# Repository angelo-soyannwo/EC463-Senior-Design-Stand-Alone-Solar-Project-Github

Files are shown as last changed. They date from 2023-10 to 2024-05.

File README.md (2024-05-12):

# Sol: An Alternative Off-grid Solar Configuration

## Quick-Start Info

### Structural Hardware

The hardware of our system consists of a frame with solar panels on either side, and a pair of reflectors in between. These reflectors slide diagonally up and down, and sideways along the rails of the frame, moved a stepper motor on either side and ball screws as the linear actuator. 3D printed components are used for interface between different parts, such as the stepper motor mount, sliding face plates, and ball screw rod attachers. Housing has also been developed for our PCBs, battery, and solar charge controller.

### Electronic Hardware

Most of our electronic pieces fit on a PCB. The light sensors and limit switches fit on the solar panels and rails of the frame respectively. The components on the PCB are: 2 Rpi Pico W's, a motor driver, buttons for Pico reset and manual motor control, 2 current sensors, and a temperature sensor. A Renogy solar charge controller is used externally to charge our battery with the solar panel, as well as power our system along with any other load.

### Control Pico Software

Our control software controls the movement of our reflectors through the stepper motors. The two stepper motors are connected in parallel to just one motor driver, so the code is made simple. Upon startup, the program moves the reflectors to their bottom-most position, where it will hit the bottom limit switch and begins tracking its position through step count. As of now, the position tracking is not an integral part of the system, since the program allows the reflectors to move upwards or downwards until they hit the limit switches; the position can be used for other purposes in the future. After startup and every ten seconds, the reflectors will check the light sensor readings, move a certain number of steps in a direction determined from the previous iteration, and check the light reading again. Based on the difference between the two readings, it will continue to move in the direction with more light or stop moving when the difference no longer passes a certain threshold. All of these parameters can be set in the software, including time between iterations and light difference threshold. Additionally, data from the light sensors are sent to our database on each iteration.

### Monitoring Pico Software

The monitoring software keeps track of charge and discharge current and voltage, and temperature of our system within the housing. It does so using two current/voltage sensor and one temperature sensor. The program first connects to WiFi, then begins the normal operation during which it sends data to our database every few seconds.

### Web Application

The web application uses a MERN stack (MongoDB, Express.js, React, Node.js). The web app takes data from our database on MongoDB, which in turn has data uploaded from our Pico servers. The user interface of the web app allows users to create an account, create arrays of our solar modules, and monitor solar panel output power, solar irradiation, and temperature across time. If any anomaly is detected, the user will receive an email such that they can check up on the system as soon as they can.

Link to Web Application: https://sol-ec-464-team-15.netlify.app/

Solar Array Id: 65539e775435e37264e3e6ff

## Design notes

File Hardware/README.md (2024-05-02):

# Hardware Documentation
## Overview
The hardware in SOL is segmented into two parts :
1. Structure & Housing
2. Electronics

The Structure & Housing consists of the solar-panels, the reflector system (mentioned in more detail below), the aluminum-gantry for mounting, and the various housings that contain the electronics & battery. 

The Electronics consist of the sensors, microcontrollers, motor driver, the Solar Charge Controller, and the PCB's that connect them. These monitor the structure, log data, then control the system based on the feedback received from the sensors.

## Structure & Housing
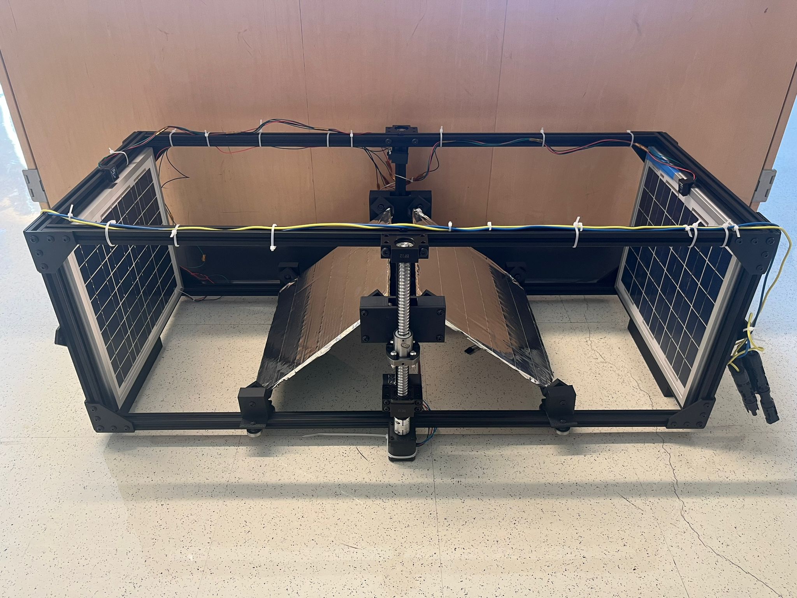
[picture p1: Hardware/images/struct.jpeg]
SOL Aluminum Structure


Above is the structure, which consists of the reflector system, the solar-panels, and the aluminum-gantry. 

### Aluminum Gantry
These are standard aluminum extrusions that can be purchased from various retailers. The original rods were 40in in length, and were machined down to an appropriate size. The size of the structure was determined by the size of the panels, and was designed such that the reflectors have enough room to cover their entire range of motion. More on this is detailed in the reflector system below. The structure is held together via aluminum brackets & screw joints.

### Solar Panels
The panels used in our design serve as proof-of-concept. As such, we were not bound to a particular power/size requirement, and thus chose panels that were provided to us by our client. The panels are 14x12 in, and have a maximum power output of 20W. 

### Reflector System
In order to explore an alternative offgrid solar-configuration, we designed a novel reflector system. The system is composed of 3D printed parts, and uses ball bearings to move about the aluminum rails. The movement of the system was inspired by 3D Printers, which use bearings to achieve precise motion. In our case, we did not need precise movement, however the notion of movement was still appealing thanks to its simplicity.

The system works as follow : 
- The stepper motors are connected to a motor driver on the PCB. 
- The motors themselves are connected to a ballscrew via a coupler. 
- The rotation of the motor turns the ballscrew clockwise/counter clockwise.
- The ballscrew is fitted onto the aluminum gantry via 3D printed mounts, and bolted joints.
- There is a printed faceplate that snaps onto the ballscrew. 
- With rotation limited, the faceplate translates upwards or downwards with the threads on the ballscrew.
- Rotational movement is turned into linear motion, which allows the connected reflectors to move radially.
- The ends of the reflectors are also connected to the gantry via sliding face-plates.

Below are renders of all the parts used in the project. These were modelled in Fusion 360 by Majid Al-Muhaideb.

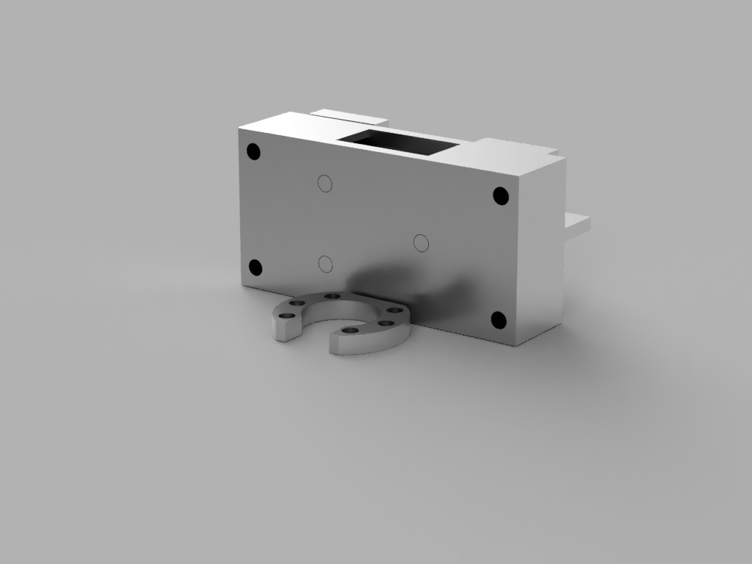
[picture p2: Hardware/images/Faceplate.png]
Faceplate Render

Faceplate Render. Snaps onto ballscrew.
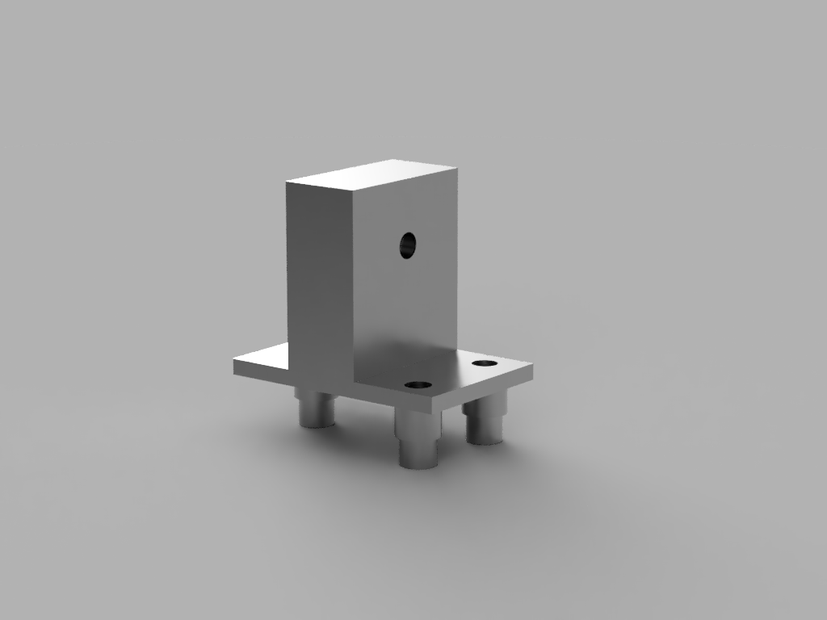
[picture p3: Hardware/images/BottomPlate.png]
Bottom Faceplate

Bottom Faceplate. bolted to the reflectors.
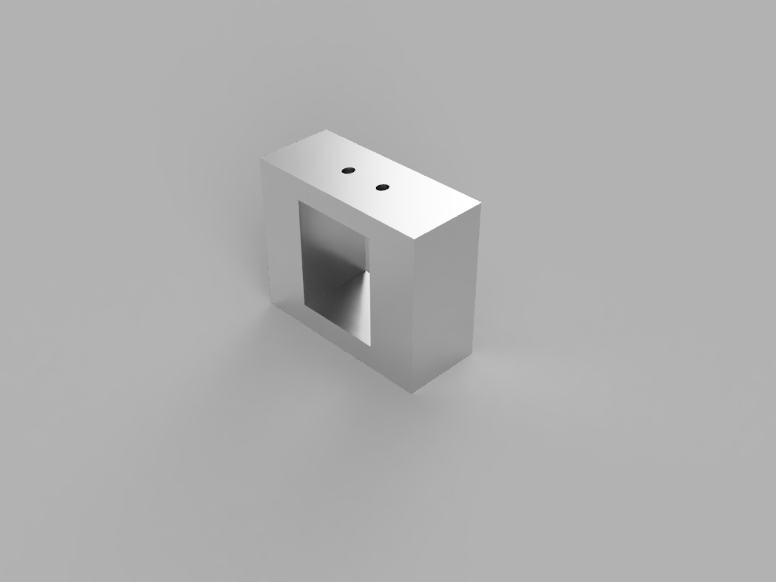
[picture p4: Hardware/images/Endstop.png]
Endstop mount

Endstop mount. Used to secure end-stops to end of the range.
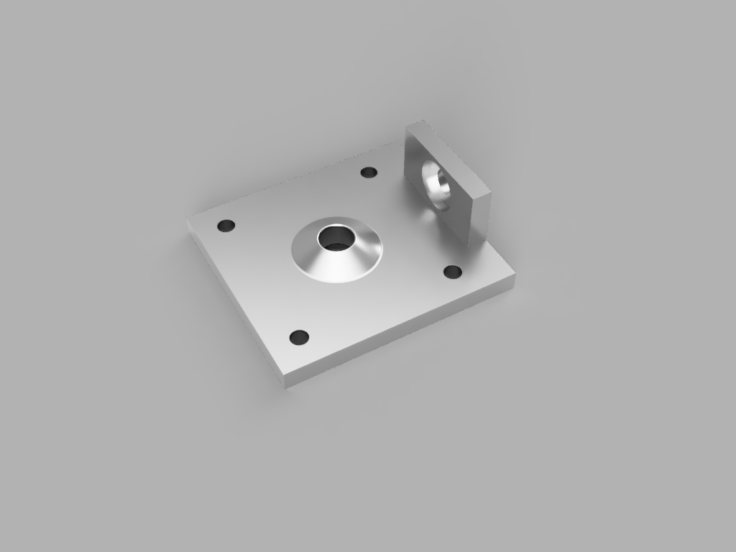
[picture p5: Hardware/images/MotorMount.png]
Motor mount

Motor mount. Used to secure motor to the structure.
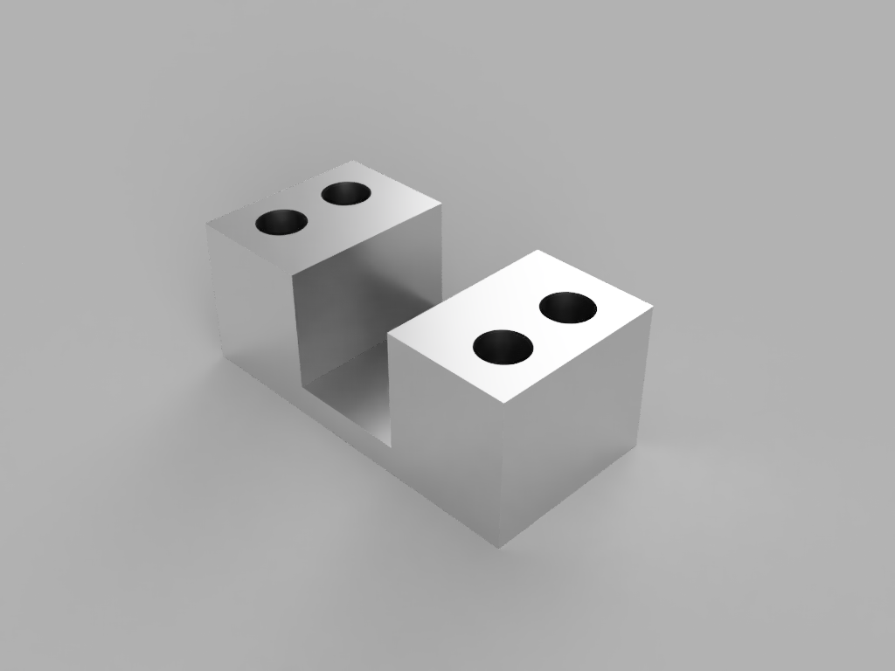
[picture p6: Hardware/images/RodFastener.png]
Rod fastener

Rod fastener. Secures rod to the structure.

The parts were printed in Black ELEGOO PLA. PETG or ABS is preferable due to their stronger mechanical properties, but both require more tuning to print properly, and are not as easy to setup as PLA. The parts dont experience a lot of mechanical stress, so it should not be an issue if used for the purposes of demonstration.

The print settings are as follows :

*Infill - 20 - 40 %*

*Infill Pattern - Gyroid*

*Print Supports - Auto, Normal*

*Walls - 3 inner walls*

Settings can be adjusted as the user sees fit, especially since each printer is tuned differently.

## Electronics
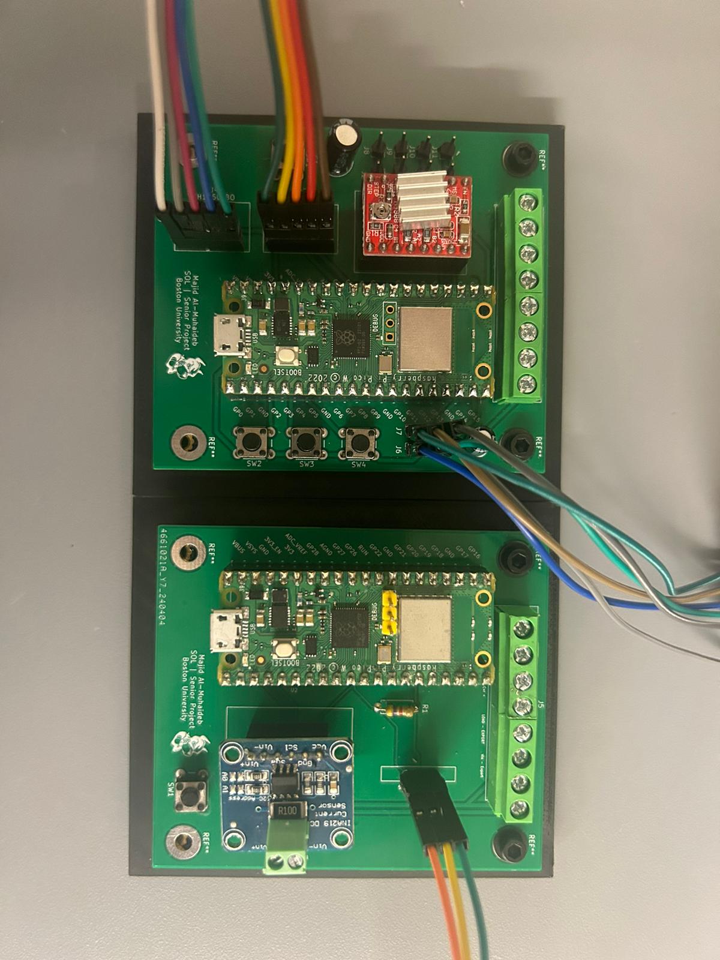
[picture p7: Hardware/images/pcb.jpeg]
Printed circuit boards


Above are the electronics used in the project. The image is a little outdated, as we've combined the two boards into one, but the electronics on them are the same, and the change is for convinence only. The electronics are divided into two subsections :

1. Monitoring : Consists of sensors that monitor current, temperature, voltage, and luminecence. The data these sensors collect is managed by a Pi Pico microcontroller.

2. Control : Consists of a motor driver that sends signals to the stepper motors. The driver is controlled by a Pi Pico Microcontroller.

The connections of these electronics can be examined in more detail in the schema folder, which contains the PCB schematic & design.

The following are some notes that should be regarded towards the PCB : 
Netlist Explanations :
 - Load + = Load from solar charge controller
 - Load - = Return path from solar charge controller. This is ground.
 - Vin P + = Positive from solar panels
 - Vin P - = Negative from solar panels
 - 3.3V_M = 3.3V from monitoring pico
 - 3.3V_C = 3.3V from control pico
 - 5V = Input from a 12V-5V converter. This is an external component
 - VCC = Vin -  from the INA219. This is 12V, and is idential to Load+.

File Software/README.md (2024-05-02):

# Software Documentation

## Overview
The software consists of three parts:
1. Reflector Control System
2. Monitoring System
3. Web Application

The control system is written in MicroPython and is uploaded to the Rpi Pico W designated for controls on the PCB. The program controls the rotation of the stepper motors to move the reflectors up and down. It does so through an algorithm to find the spot at which incident light on the solar panels is optimized. The program also simultaneously sends data from the light sensors to our MongoDB database.

The monitoring system is written in MicroPython and is uploaded to the Rpi Pico W designated for monitoring on the PCB. The program uses sensors to continually monitor the current and voltage of the solar panel output, and the temperature of our system. It sends these data to our MongoDB database. Users also receive an email notification for any detected anomalies.

The web application uses a MERN stack. It takes data from our MongoDB database and displays it in a visually pleasing way on the appication. Users may create an account, log in, add solar arrays, and view trends on their solar array data.

## Reflector Control System
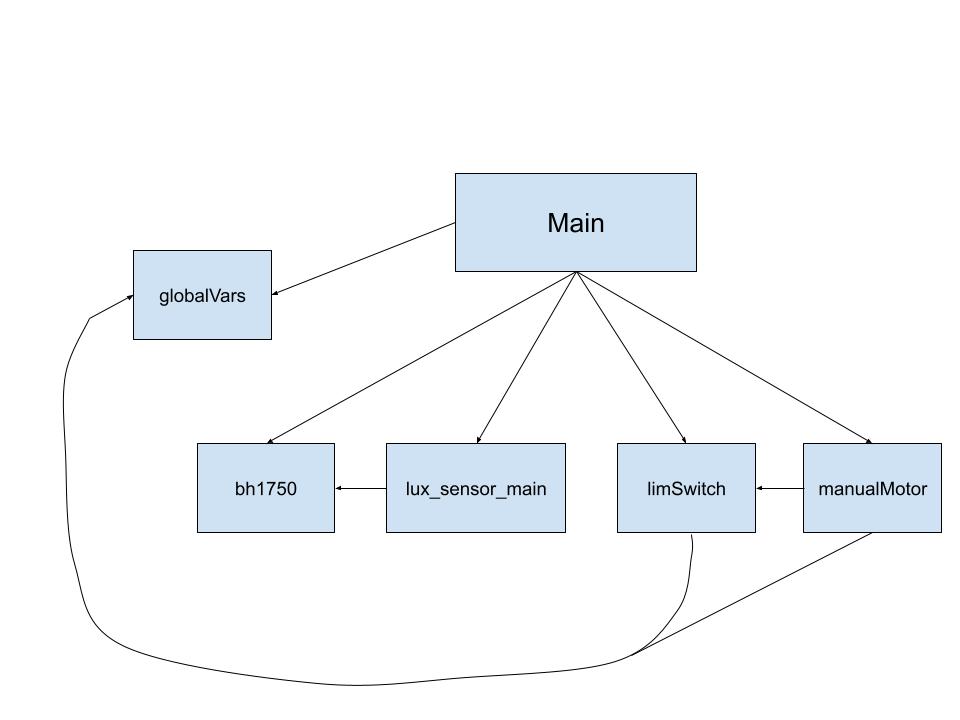
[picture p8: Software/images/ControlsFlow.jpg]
Controls Module Flow Diagram


Above is the module flow diagram for our control system.

### main.py
The main.py program of the control system begins by initializing all components necessary. It imports all of the other modules, initializes the I2C light sensors, and initializes the GPIO pins used for the motor driver. Its defined functions are RotateMotor, findLight, posRst, and main. RotateMotor simply consists of the stepping of the motor, and checks for the swHit flag that indicates that one of the limit switches has been hit, in which case it will exit the function, or continue it if the direction of rotation is away from the limit switch hit. The findLight function is the algorithm the program uses to find the position of the reflectors to optimize the light the solar panels receive. In this algorithm, the reflectors first reads the light sensor at its current position, moves up a set amount and reads the light sensor again, and compares the two readings. It continues to move up and down in diminishing distances until it settles at a position in which the difference in light between consecutive positions no longer passes a certain threshold. The posRst function is called upon initialization and moves the reflectors down until they hit the bottom limit switch, from which it can begin tracking its position in software through steps rotated from the bottom. The control system currently does not utilize this position tracking and instead only uses limit switches to prevent over-rotation, but the position tracking may be used for analysis by a future team. The main function puts all of these other functions together and is run on startup, first connecting to WiFi, then looping through the other functions. Additionally, the entire module checks for the manualMode flag throughout the program, in which case it will enter manual control mode.

### lux_sensor_main.py
This module sends the light sensor data to the database, and is called by the main module. The function calculate_solar_irradiation converts the sensor data in lux to solar irradiation in W/m^2 and the readPower function calculate the power produced by the solar panels. The connect_to_wifi connects to WiFi with the SSID and password as parameters. The functions createOne, findOne, pushOne,and updateOne create a new "day" on the database, finds the right day, pushes data to the right dictionary, and updates data already in the database. The luxMain function does these things with regards to the light sensor readings.

### limSwitch.py
This module holds the interrupt and interrupt handler for the bottom and top limit switches. The limit switches are pulled high, normally open, and triggers the interrupt upon the falling voltage, with its com connected to ground. The handler immediately disables the motor, checks which limit switch was hit, and sets the swHit flag to the right value--1 for the bottom switch, 2 for the top switch. This flag is set back to 0 upon moving away from the limit switch in either the main module or the manualMotor module.

### globalVars.py
This module simply keeps track of the position tracking of the stepper motors, the swHit flag for the limit switches and the manualMode flag for the manual control mode. A separate module is used to make updating these variables easy across all of our modules.

### bh1750.py
This is an open source module which consists of a class for the BH1750 light sensor. This class is primarily used to initialize our light sensors and read sensor values.

## Monitoring System
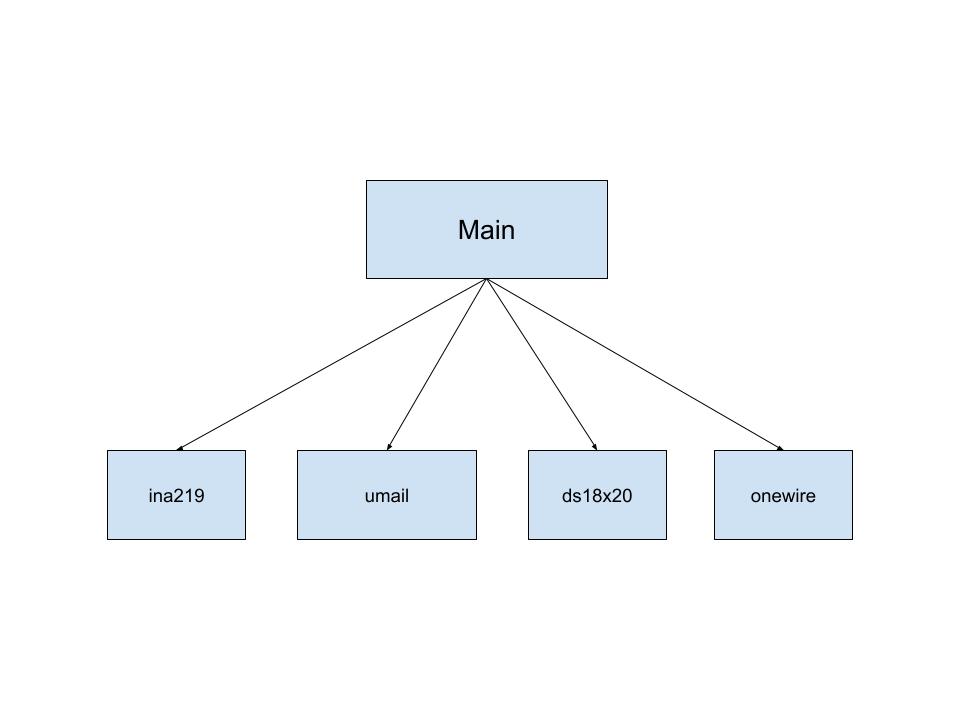
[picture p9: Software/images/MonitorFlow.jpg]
Controls Module Flow Diagram


Above is the module flow diagram for our monitoring system.

### main.py
The main module of the monitoring system initializes I2C for the current/voltage sensor, and initializes the temperature sensor with the use of the onewire module, since there is only one data bus for the temperature sensor (its other pins are for power and ground). The main module then has a collection of functions used for interfacing with our database, for creating, finding, and updating data fields. This also includes anomaly tracking. The main function uses these functions to continually read data from the sensors, converting the value to be sent to the database, and sending the data to the database. It also checks if the current or voltage reading is outside of a certain threshold, in which case it will send the anomaly notification email.

### umail.py
This module contains a class for an SMTP client for sending email in MicroPython (MIT license; Copyright (c) 2018 Shawwwn <shawwwn1@gmail.com>). This module is used for sending detected anomalies in our main module.

### onewire.py
This is a one-wire driver for reading data with a digital GPIO pin (MIT license; Copyright (c) 2016 Damien P. George). We use this class to initialize our temperature sensor.

### ds18x20.py
This class initializes our temperature sensor and read temperature (MIT license; Copyright (c) 2016 Damien P. George). Specifically, we use the scan, convert_temp, and read_temp functions in our main module.

### ina219.py
This module is an open source library for the current/voltage sensor. Specifically, we use the getBusVoltage_V and the getCurrent_mA functions in our main module.

## Web Application
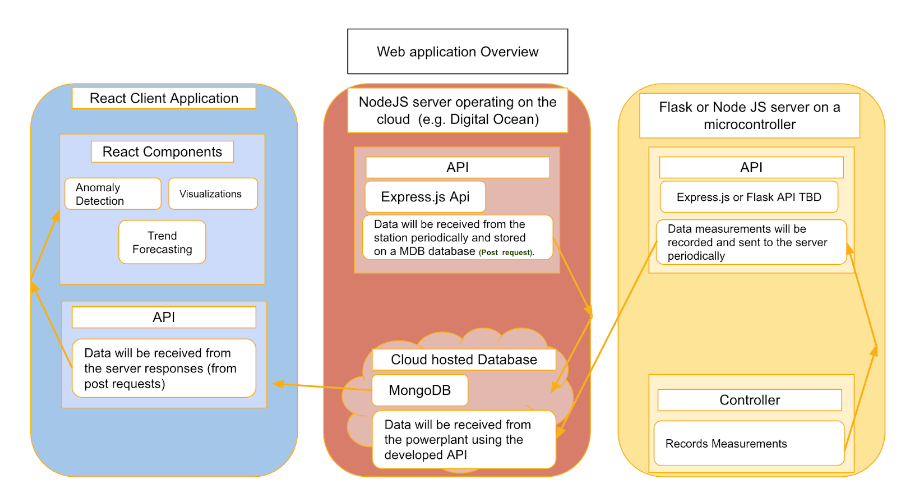
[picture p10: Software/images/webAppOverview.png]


Above is the overview diagram for our web application.

### Overview
The web application consists of a MERN stack app, which includes MongoDB, express.js, react, and node.js. It will be hosted on a cloud hosting provider like digitalOcean or Heroku. The app utilizes a cluster on the MongoDB Cloud Atlas hosting platform to store the data from the Pico W. In this manner, the microcontroller is capable of transmitting data to the database directly from any IP address, as per the configuration chosen on the web platform. The web application utilizes an express.js server for its server side. This server manages all API calls made from the front end (React) side, including get, post, put, and head requests. The express.js server establishes communication with the database housed on our cloud platform. ExpressJS, a framework derived from Node.js, is an asynchronous runtime environment that facilitates the development of network applications. The client side of the system will comprise a client application developed using the react.js framework, which is structured as HTML. The react client will interact with the express.js web server by utilizing the Axios javascript requests module to initiate requests. Subsequently, the web server will transmit data to the client to render and present it to the user.

### Installation
Please find details on how to run the web application from scratch in (./Web_App/README_WebApp.md).

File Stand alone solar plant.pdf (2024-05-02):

Senior Design Project 2023-2024

Title: Development of a monitoring and control system for operating a stand-alone solar energy plant, with a hybrid energy storage system using lithium-iron-phosphate batteries and super-capacitors

Stand-alone solar energy plants with energy storage capacity are used in many applications in the US and abroad where manual operation is difficult or not desirable. While these plants do not require manual operation, energy storage through lithium-ion batteries becomes essential for meeting energy needs. However, this introduces reliability concerns as well as safety risks of fire or explosion. A monitoring system is needed to check the operation of the system (power output) and the status of the batteries with respect to their charge level, the rate of charging, and charge dissipation. Recording logged operational data and automating trend analysis for anomaly discovery is also critical. A hybridized energy storage process is used in combination with electric double layer super-capacitors and lithium iron phosphate batteries in cascaded operation with a DC bus bar as shown in Fig.1.

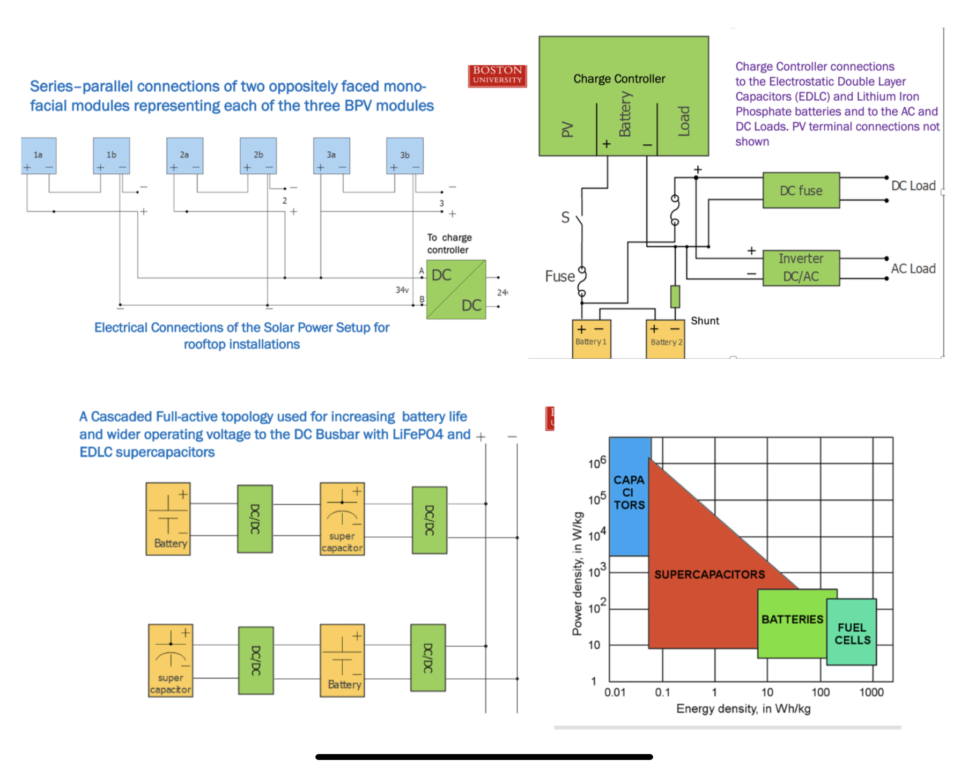
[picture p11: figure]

Last year a senior design project team developed a solar energy system to which we have added a cascaded hybrid energy storage device. We need a remote monitoring and control system for its operation as a stand-alone solar plant to ensure reliability and safety. Determining the plant power output as a function of the solar irradiation incident on the solar panels and maintaining a record of the charging status and the rate of charging and dissipation are of critical importance.

The solar energy system is currently installed in the lab (PHO 109) will be used for a lab-instruction component of the solar energy system classes for students enrolled in the class to have hands-on experience in the operation of stand-alone PV plants.

The senior design team working on the project this year will be provided with the solar panels, charge controller, batteries, super-capacitors (EDLC and Li-ion batteries). The team will design and assemble the system with electrical integration including the monitoring and control system for remote operation (within 5000 ft). The team will demonstrate the operation and deliver the control and monitoring devices used in connection with the solar plant with detailed instructions.

Customer: Malay Mazumder, Research Professor, ECE Department, email: mazumder@bu.edu

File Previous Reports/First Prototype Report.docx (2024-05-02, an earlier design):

Memo

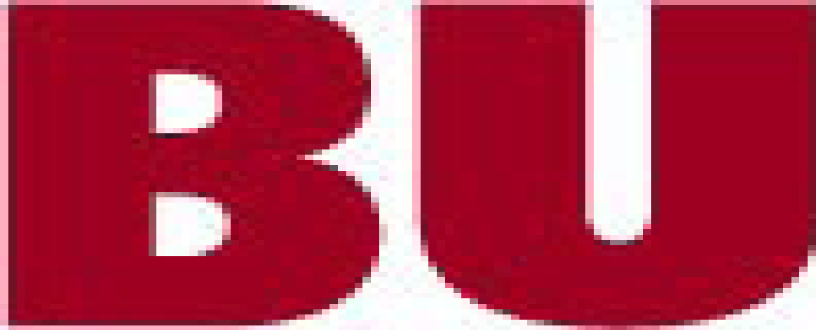
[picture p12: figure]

Senior Design

ENG EC 463

To: Professor Pisano

From: Alexa Wiencek, Angelo Soyannwo, Majid Almuhaideb, Rahat Mahmood, Steven Cheng

Team: 15

Date: 11/16/16

Subject: First Prototype Report

1.0 Hardware Prototype

1.1 Setup

The setup of our hardware prototype consisted of a pair of solar panels connected back-to-back in series (to conceptually represent the bifacial solar panels) in a circuit with a solar charge controller, lead acid battery, battery monitor, and a small light bulb serving as a test load.

1.2 Test Procedure

Once the circuit is fully connected, the readings on the solar charge controller and battery monitor can be read. The light bulb should be lit as well, but is most likely being powered by the battery rather than energy from the solar panels. Placing one of the LED light sources in the lab against one of the solar panels and turning it on demonstrates how the circuit behaves when it is exposed to more light.

1.3 Measurable Criteria

A successful test is marked by accurate readings being displayed by the solar charge controller and battery monitor. In addition, the solar panels should be able to power the load (lightbulb) as well as charge the battery with excess power when the LED lightsource has been turned on.

2.0 Software Prototype

2.1 Setup

To demonstrate our current prototype of the web server, all the setup required was a laptop. Two terminal windows were used to open the application and backend server.

  2.2 Test Procedure

After starting the application, it was demonstrated how to sign up, log out, and log in a user. It was then shown how to add and update solar arrays in the database. Our demonstration of the server also included how a user would add a solar array to their profile. To demonstrate how our remote application will update in real time later on, database values were then changed and the webpage was refreshed, displaying the updated values.

  2.3 Measurable Criteria

The ability to store login information as well as other information linked to a user profile such that it can be accessed after logging in is one of our main measures of progress. Additionally, both being able to access and update solar arrays in the database, as well as the server displaying the most up to date information on an array.

3.0 Conclusions

Good progress has been made on the remote application aspect of this project, and it will continue being improved on for the remainder of this semester as well as in the second half of the year. In terms of hardware, the team has gained a better understanding of the different components of putting together a small scale solar power plant. Now that our project definition/what our client wants has been finalized we will begin making noticeable progress in the hardware area, and aim to catch up to the software side of the project. Most importantly, although we need to work quickly, our priority must be on ensuring safety when working with batteries/supercapacitors.

Progress also has been made on the circuitry of control system for the reflector and monitoring system. Moving forward we will keep working on those and come up with a some sort of small housing to keep the circuitry of our monitoring and control system.

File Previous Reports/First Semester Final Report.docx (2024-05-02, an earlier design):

# Boston University

# Electrical & Computer Engineering

# EC463 Senior Design Project

# First Semester Report

Sol: Solar Power Plant with Remote Monitoring Application

Submitted to

Prof. Malay Mazumder

Boston University

8 St. Mary’s St Boston, 02215

(617) 353-0162

mazumder@bu.edu

by

Team (15)

SOL

Team Members

Majid Al-Muhaideb majidmuh@bu.edu

Rahat Mahmood rahat73@bu.edu

Alexa Wiencek awiencek@bu.edu

Oluwaseun Angelo Soyannwo seun@bu.edu

Steven Cheng stcheng@bu.edu

Submitted: December 9, 2023

#### Table of Contents

Executive Summary 2

1.0 Introduction 3

2.0 Concept Development 4

3.0 System Description 5

4.0 First Semester Progress 7

5.0 Technical Plan 9

6.0 Budget Estimate 11

7.0 Attachments 12

7.1 Appendix 1 – Engineering Requirements 12

7.2 Appendix 2 – Gantt Chart 14

7.3 Appendix 3 – Other Appendices 16

# Executive Summary

Solar Power Plant with Remote Monitoring Application

Team Number 15 – SOL

Off-grid solar plants, solar power plants that work independently from the grid, are among the most promising solutions to rising alternative energy demand. These systems require an energy-storage element, usually a LiPo or SLA battery, and need additional safety considerations. Our client contracted us to work on a plant monitoring and control system that keeps track of key metrics in various parts of the plant, with an emphasis on battery safety. We have also been tasked with creating a remote-application that streamlines remote plant-monitoring. Our proposed technical approach involves the iteration of monitoring and control systems on a small-scale solar plant model. Our goal is to provide the client with a robust, flexible system that can be easily adapted to most off-grid configurations. Additionally, our client’s proposed system involves the use of Electric Double Layer Capacitors [EDLC] as an energy storage supplement for high-current loading, as well as Bifacial modules as our solar panels; both unique considerations introduce the need for a tailored plant-management system.

# 1.0 Introduction

Environmental sustainability is among the most important and heavily researched topics in the 21st century. An overreliance on polluting sources of energy has placed our world on a destructive trajectory that threatens to eliminate swathes of nature and wildlife. The need for alternative power to replace non-renewable sources of energy encouraged the development of many different possible solutions, with solar among the leading technologies in sustainable power. Solar can be used in a variety of configurations in combination with the grid, from backup power to net-metering solutions. Off-grid configurations of solar-plants distinguish themselves from these variations by bypassing the grid connection, allowing users to create a self-reliant mini-grid disconnected from mains power. These configurations of plants allow users in rural or inaccessible areas to utilize sustainable power without the restrictions that accompany grid-connected power. These off-grid systems have several setbacks however and require additional engineering considerations, such as the need for batteries to store excess energy, as well as the safety systems that govern them and the plant. Our client, Professor Malay Mazumder, is working on a proposal to build such a plant on the roof-top of BU buildings. This proposal is in its infancy, and we have been contracted to assist with modeling the solar-plant and creating a management system that monitors and controls the plant.

As previously mentioned, off-grid plants require additional considerations to operate safely. Batteries are required to power loads during sun-absence periods, such as on cloudy days or during the evening, and must be constantly monitored in order to detect anomalous behavior that may cause damage. Furthermore, the condition of the solar panels must be constantly monitored in order to prevent reduced power or blackouts resulting from contamination or deterioration of the panels. These considerations in both safety and reliability introduce the need for a flexible and robust monitoring and control system that ensures the constant operation of the plant. Due to the project being in its early phases, we’ve also been tasked with creating a model that we will use as our benchmark for testing our plant management system. Additionally, our client requested that we integrate remote-monitoring considerations into our design, which we aim to achieve via a web-application that displays key-plant metrics.

Our goal is to deliver a robust, flexible management system that can be adapted for larger configurations of off-grid solar plants and can be remotely monitored, reducing the need for physical presence near the plant. Our solution will allow the client to develop his proposal and assist in ensuring the safety and reliability of the final product and provide him with insight into what pain points could cause delays in his proposal. Our approach in this project will be to build a bifacial solar module model, complete with a charge controller and battery, and fit our management system to this model. Additionally, we will research and implement an Electric Double Layer Capacitor energy storage layer to assist the plant battery system with abrupt high-current spikes that may cause battery degradation or damage.

# 2.0 Concept Development

The goal of our client is to develop a means to reduce the carbon footprints of buildings at Boston University. This will be achieved through the installation of a solar-power plant. The power plant will consist of an array of bifacial solar panels in combination with a hybrid battery capacitor energy storage system. Each panel will have a reflector that changes position throughout the day, to maximize incident solar irradiance on the panel faces. The primary problem our client needs us to solve is ensuring the continued safety, particularly battery safety, of the solar-plant. Lithium-ion batteries, the battery type that the final system will use, are known to enter a process known as thermal runaway if they overheat, are overcharged, or are short circuited, causing fires or explosions. To prevent battery failure and other dangerour anomalies, our team is developing a monitoring and control system for the solar array. The monitoring system will have several sensors including measurements for voltage, current, and temperature. We have also received the request to design a remote application with a minimum range of 5000 ft that shows the data collected by the monitoring system. For this, a microcontroller connected to the monitoring system will send data to a web-based application to achieve both quick update times and sufficient operating distance.

It is important that proper operation of the plant can be verified remotely at any time. For this, our team is developing a remote application on a web server. This allows the state of the plant to be checked from a distance, as the server will continue to update its display of key system metrics. Using a web server makes accessing the remote application over a greater range away from the solar-plant itself possible. We chose this approach over an application based on bluetooth or similar wireless signals, as the functional range where the remote application would be accessible would be far below what we need to deliver.

The monitoring system being developed by the hardware side of our team is composed of individual sensors and a pico w. Putting together the monitoring system rather than opting for an off the shelf solution allows for greater customization in the design as well as ensures we are able to send monitored data to our remote application. Our client’s lab space already had a few products that measure some of the metrics we are monitoring, but these devices were not compatible with hardware from other brands and did not allow data to be exported (only printed to the led display). While this works perfectly fine for in-person monitoring, in order for the system to safely operate without direct supervision, it requires remote monitoring at all times. The sensors chosen for our system can easily connect to the pico w data in pins, allowing a straightforward flow from data collection to the remote display.

# 3.0 System Description

Our system will consist of a solar power plant, monitoring system, and web application. The solar power plant will consist of an array of 6 bifacial solar panels connected in series with one another, an energy storage system, and a charge controller. Each bifacial panel is rated for 40W output power and will have a reflector module that sits underneath it and rotates throughout the day to maximize incident solar irradiation. The solar array will be connected to a hybrid energy system consisting of a set of batteries and supercapacitors. The hybrid system exists to respond to different changes in the needed output energy. When a quick spike of energy is needed, then the supercapacitors can be discharged, but when a more stable increase is needed, the batteries will discharge. We are currently planning to use some 300 farad capacitors with the Lithium polymer batteries that our client has ordered. The system will be connected to a charge controller which will ensure that the battery is operating within the specified current, voltage, and charge level limits.

Figure 1. System Overview

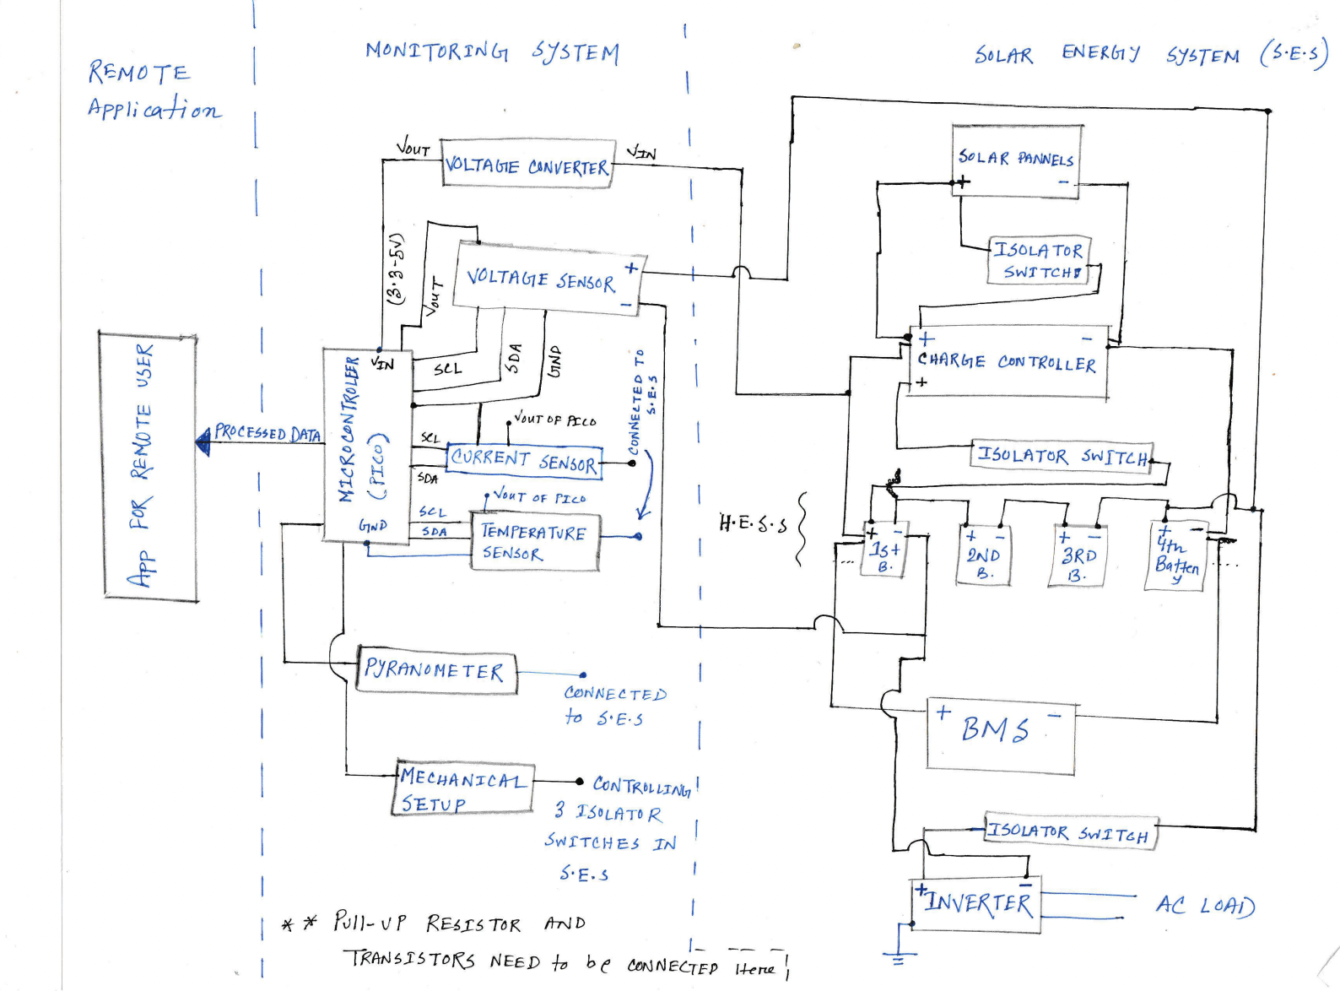
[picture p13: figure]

Our System will have three largely parallel sections: a remote application, a monitoring system, and a solar energy system. The monitoring system will be carefully connected to the solar plant and we will install the necessary safety components (i.e. relays and fuses.)

The monitoring system will consist of a Raspberry pi pico w and pin extension board connected to an array of sensors measuring power plant data (as of now we will be reading current, voltage, temperature and solar irradiance). The pico will make use of several python networking libraries (i.e. network and urequests ) to connect to the Internet and send sensor data to our database hosted on the Mongodb Cloud Atlas hosting service (via the services data API). We will use sensors to measure the voltage, current, temperature, and solar irradiation. The monitoring system will control isolator switches that isolate the batteries from the rest of the system during potentially dangerous operational levels. To read the values from these sensors we will use GPIO pins on the pico and Python libraries such as machine and sensors.

The web application will be a MERN (MongoDB, express.js, react, and node.js) stack application hosted on a cloud hosting platform such as digitalOcean or Heroku. In order to store the data from the pico we will be using a cluster on the MongoDB Cloud Atlas hosting platform to host our database. This way our microcontroller can directly send information to the database from any IP address (as we selected that setting on the online platform). The server side of the web application will be an express.js based server. It will handle any get, post, put, or head requests made from the front end (react) side. The express.js server will interact with our cloud hosted database. Express js is based on node.js is an asynchronous runtime that helps developers to build network applications. The client side will consist of a react client application made of react.js formatted html. The react client will make requests to the express.js web server using the axios javascript requests library. The web server will then send data back to the client to be rendered and displayed for our user.

The sensor data stored by our monitoring system needs to be used for trend analysis and anomaly detection. We will be using MongoDBs built-in chart embedding SDK in order to embed charts into our trend analysis page. Anomalies will be detected via a control loop on the pico that has set thresholds for normal operation. When these thresholds are passed, a notification will be sent to our users. As of right now we are planning to use Twillio web services for text messages in addition to the MicroPython umail library.

Figure 2. Software Overview

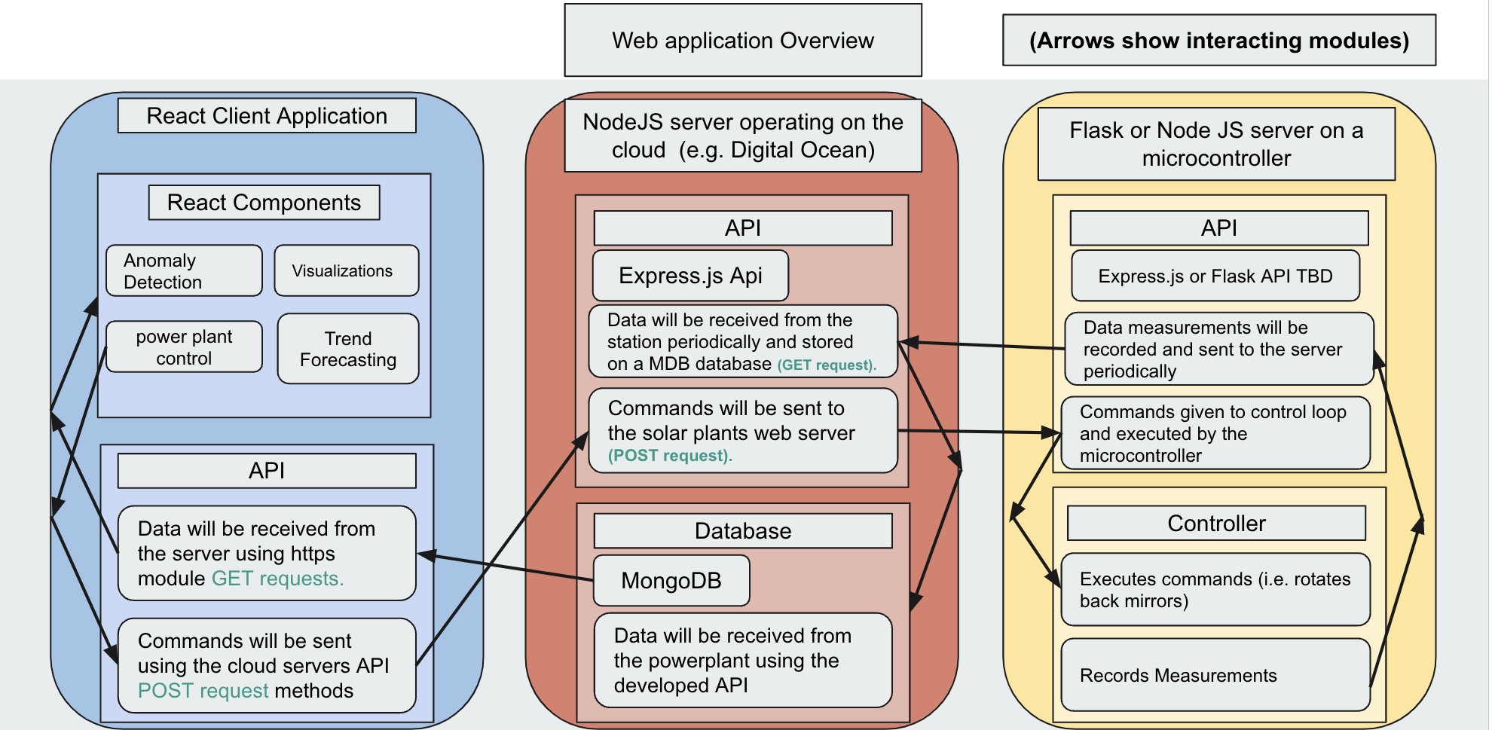
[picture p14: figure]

We will be using a react native client application that will be hosted on a cloud service provider and served to a user’s browser. This website will interact with a nodeJS server application running on the cloud which will handle logins and retrieving data from our cloud hosted MongoDB database. The MongoDB database will be updated by a Raspberry pi pico using the Cloud Atlas Data API.

Regarding the UI, our goal is to have as simple of a UI as possible. For our homepage We are going to have a central column that displays the data which our client wants. Next to that we will have a series of buttons that will allow our user to perform tasks such as adding additional solar arrays to his page and creating new solar Array instances.

Figure 3. UI

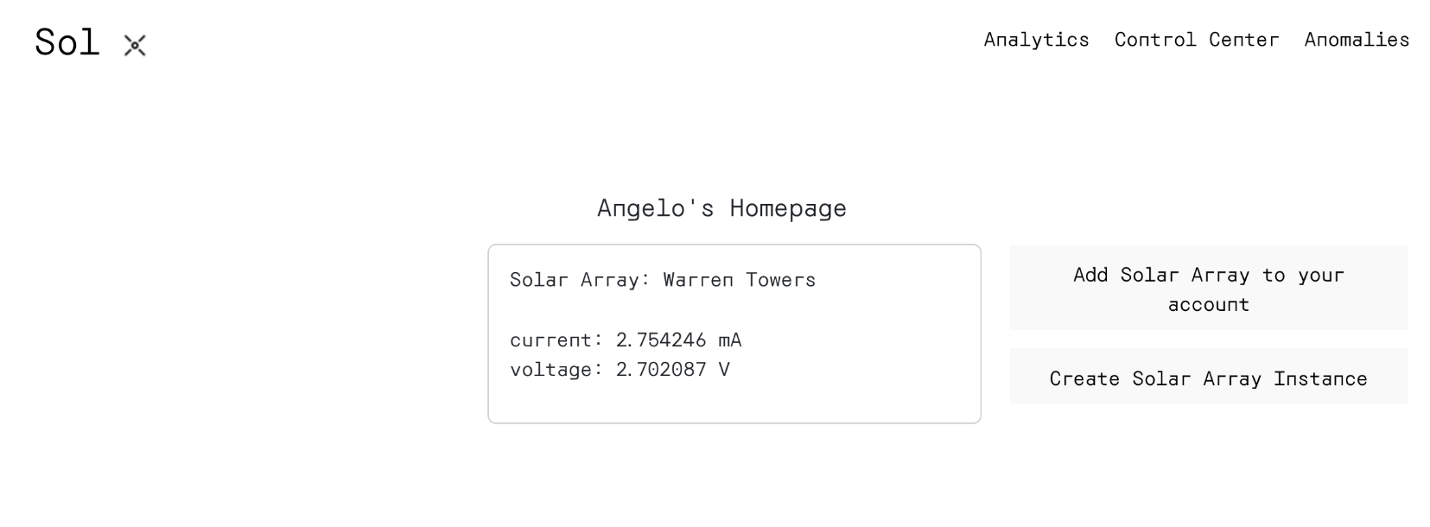
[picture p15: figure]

# 4.0 First Semester Progress

During the first few weeks we developed an overview design concept that laid out the four main subsystems that would connect with each other. These were the physical plant, the monitoring system, the web application, and the control system. According to our project description, the physical plant was to be handled externally by our client such that we would focus only on the monitoring system through an embedded system using a Raspberry Pi Pico W, and a web application connecting to a server which the Pico W would also connect to. At this time, the control system was the only subsystem still abstractly defined, not strictly confined within a means such as a web application or physical system. We were unable to reach our client to ask for details and confirm our initial design during these first weeks.

During the Shark Tank, we gained valuable insight on additional considerations such as multiple temperature sensors in different locations of the plant, off-the-shelf solutions, and the obstacle of high power and current. During a meeting with our client, we learned that our project would encompass not only the monitoring and control system, but also the physical plant. Our client revealed that the solar plant had actually not been assembled, and that his current research team was working on its development. We decided that it was best to also include this collaborative responsibility in our overall project in order to ensure successful integration of all parts. The control component of our project was also defined to be strictly relating to the reflector system, not operation of the solar plant itself; the shutoff of the plant during anomalies was to be handled by the off-the-shelf charge controller.

The following week, our team discussed our new distribution of work. Alexa, Majid, and Rahat were to join the research team’s efforts in the solar plant assembly, while Angelo and Steven would begin development of the web application. Detailed below is the progress made on the hardware side and the software side.

4.1 Hardware Progress:

On the hardware side, we were split into two main workstreams, one focusing on creating a solar-plant model in collaboration with the client research team, and another centered around creating our management system prototype.

Plant Management Workstream

Three deliverables were worked on over the course of the semester. First, the monitoring system prototype, shown in Appendix 7.3. This prototype is the first iteration of our monitoring system, able to measure both voltage (12V) and current (1A) in various parts of the plant. The second deliverable is the control-system, also shown in Appendix 7.3 which uses data from its monitoring circuitry to adjust a stepper motor’s rotation that controls reflectors in the plant, which maximizes solar-irradiance.During the first iteration of this design, stepper motor was able to rotate total 68 steps clock-wise and 68 steps counter-clockwise based on the three time slots.

Plant Model Workstream

After extensive deliberations with our client and his team, we finalized the design for a small-scale solar power plant prototype which is the third deliverable. This system incorporates two solar panels configured in a series arrangement, mounted back-to-back. The panels are linked to a charge controller, a pivotal component in emulating a real-life, off-grid solar system. This setup centralizes the system, allowing for a precise simulation of real-world operational conditions. This model was demonstrated during our design review, and was a success. However, during our review, the battery was accidentally shorted and an audible hiss was heard, which was presumed to be caused by the hydrogen gas attempting to escape the enclosure due to the massive amount of current discharge resulting from the short. This incident brought into light the importance of incorporating a fuse for enhanced battery protection, as well as the need for a safety procedures document to ensure proper handling of energy-storage devices.

The schematics of the deliverable can be seen in Appendix 7.3

4.2 Software Progress:

Angelo has worked on developing a functioning web application front end with which users are able to create an account and add specific solar arrays to their account with solar array IDs, and monitor solar plant statuses. Angelo also worked on the back end such that the web page connects to our MongoDB database. During our prototype testing, we were able to demonstrate a functioning front and back end to display sensor values updated manually on our database. Throughout this time, Steven has also worked on the back end of the application, developing a dummy voltage and current reading function implemented in a data-post function all on the Pico W. In this way, the Pico acts as a localized server that communicates with the database, updating data incrementally with a set time. The dummy data reading functions will eventually be updated to incorporate our sensors. By the end of the semester, our team demonstrated the successful use of the web application, including creation of an account, login, adding and solar arrays to the account, and monitoring readings now automatically updated from the dummy sensor.

4.3 Future Plans:

In the last few weeks, we developed plans for next semester. On the software side, tasks include the implementation of the data analytics capabilities, and integration with the sensors. On the hardware side tasks include the incorporation of the proposed supercapacitors and LiPo batteries, and integration of the reflector system.

# 5.0 Technical Plan

5.1 Hardware:

The client team arranged a number of tasks for us to work on outside the scope of our project. These tasks are meant to develop the project to a level where we can focus on creating a practical management system. The tasks are as follows :

Task 1. Structure for solar reflectors

A physical structure will be developed to hold reflectors, using TSLOT Aluminum and various small parts. The development process includes designing in SolidWorks, prototyping with a 3D printer, and conducting tests. The design will be evaluated for its capacity to hold reflectors weighing less than 500 grams and for its functionality in holding and rotating the stepper motor as per specifications.

Task 2. Determine the torque for control system

Nema 17 itself can provide maximum torque up to 0.5 Nm and to effectively gauge the torque required for maneuvering a solar panel reflector via a stepper motor and Raspberry Pi Pico, a strain gauge torque sensor shall be employed and calibrated, ideally attached to the motor's shaft. If necessary, incorporate an Analog-to-Digital Converter (ADC) like the HX711 to bridge the sensor's analog output with the Pico's digital input preference. Program the Pico for data acquisition from the sensor, ensuring GPIO pin setup and coding align with the task. Execute tests to record torque values during motor operation, and analyze this data to ascertain the needed torque range. Modify our setup or select an alternative motor based on these insights, consulting component datasheets and manuals for precise execution.

Task 3. Integrating various features into control system

A light sensor, such as the BH1750 shall be mounted externally on the black box housing of Raspberry Pi Pico to monitor light conditions to put the RPi into sleep mode for power savings and ensuring it's weatherproofed for outdoor use. Additionally, an anemometer shall be integrated with the Pico, selecting either a digital pulse output or an analog voltage output model based on our system's compatibility and ease of interfacing. Preferably use a digital anemometer for a more straightforward connection with the Pico. This configuration will be tested outside under various weather conditions.

Task 4. Integrating Temperature sensor into monitoring system

DS18B20 temperature sensor shall be integrated to monitor a LiPo4 battery's temperature as for long-term storage, keeping the battery in a temperature range of about -20°C to 25°C (-4°F to 77°F) is recommended. The Rpi shall be programmed to read and integrate temperature data with existing INA219 measurements. This system shall be tested and calibrated with the prototype solar plant for accurate monitoring, ensuring safe and reliable battery operation and remote data access.

Task 5. Designing a reflector for solar panels.

An easy and efficient reflector shall be designed for the solar panels to enhance its energy absorption and overall efficiency.. The design shall be focused on optimizing the shape and angle to maximize sunlight capture, using reflective materials that are durable and weather-resistant. It shall be ensured that the design is easily adjustable for optimal solar tracking throughout the year.

Task 6 Building a Plant Model

Due to the project being in its early stages, we do not have a plant on which to test our management system. As a result, we have been tasked with creating an approximate scaled model of the final system that we can design our project around. The plant uses all the necessary architecture for an off-grid solar system, including a charge-controller, an energy storage element and a BMS.

5.2 Software:

Task 1. Integrate MongoDB Chart SDK into react application

Display chart data for the logged in user’s solar arrays to the trend analysis page.

Task 2. Add trend Analysis capabilities

Our client wants to be able to monitor and forecast certain performance metrics based on past data. We will need to integrate these capabilities into the web application.

Task 3. Add Notifications

We must be able to notify our users of anomalous behavior through text and email. We will integrate this into the monitoring system using the python umail library and tentatively twilio web services.

Task 4. User feedback and iteration

Our users will test the product and give us feedback to iterate and improve.

# 6.0 Budget Estimate

Item | Description | Cost
1 | Solar Modules | $75.00
2 | Charge Controller | $12.00
3 | Batteries | $40.00
4 | BMS Shunt | $90.00
5 | Fuse Holders | $10.00
6 | Crimp Terminals | $18.00
7 | SLA Charger | $12.00
8 | Wires | $20.00
9 | Connectors | $15.00
10 | Raspberry Pi | $7.00
11 | INA219 | $3.00
12 | RTC-DS3231 | $3.50
13 | A4988 Stepper | $7.00
14 | Nema 17 stepper motor | $14.00
| Total | $326.50

Since our client has been working on this proposal before contracting our team, we were given access to multiple key items that assist us in the creation of the solar model, which are highlighted in gray. The monitoring and control elements, however, are new to this project and must be sourced either via our client or through the senior design budget. Additionally, due to the iterative nature of our project, this budget does not encompass total expenditures, and is expected to grow. The solar panels, which constitute the majority of the cost, were given to us by the client, which means our future increases to the budget shouldn’t cause any planning issues.

# 7.0 Attachments

# 7.1 Appendix 1 – Engineering Requirements

Team #15 Team Name: SOL

Project Name: Solar Power Plant with Remote Monitoring Application

Requirement | Value, range, tolerance, units
Data storage | 100mb of time series data storage
Power | 40-80W
Current | 2-5 Amps
Monitoring System | Capable of measuring up to 26V, 2A, and 45° C. Able to successfully connect and send data values to the web server.
Control System | Able to move reflectors through the desired range of angles. Provides at least 0.5 Nm of torque.
Reflectors | Can reflect additional light onto the solar panels to increase energy absorption and overall efficiency. Must have position adjusted throughout the course of the day in response to the position of the sun.
Number of concurrent users on the web application | 10-15
Number of creatable Solar Array instances in our database | 100+
Trend Analysis | Time series data for the operation of the solar plant must be present in the front end application as charts.
Notifications | The system must notify users through at least email of anomalous behavior.
Lithium polymer battery and supercapacitor hybrid energy storage | The system must use a hybrid lithium polymer and super capacitor configuration to store energy.
Safety | The solar plant will make use of a battery monitoring system (the one provided with our client’s battery), as well as 3A fuses in order to meet our client’s safety standards.

# 7.2 Appendix 2 – Gantt Chart

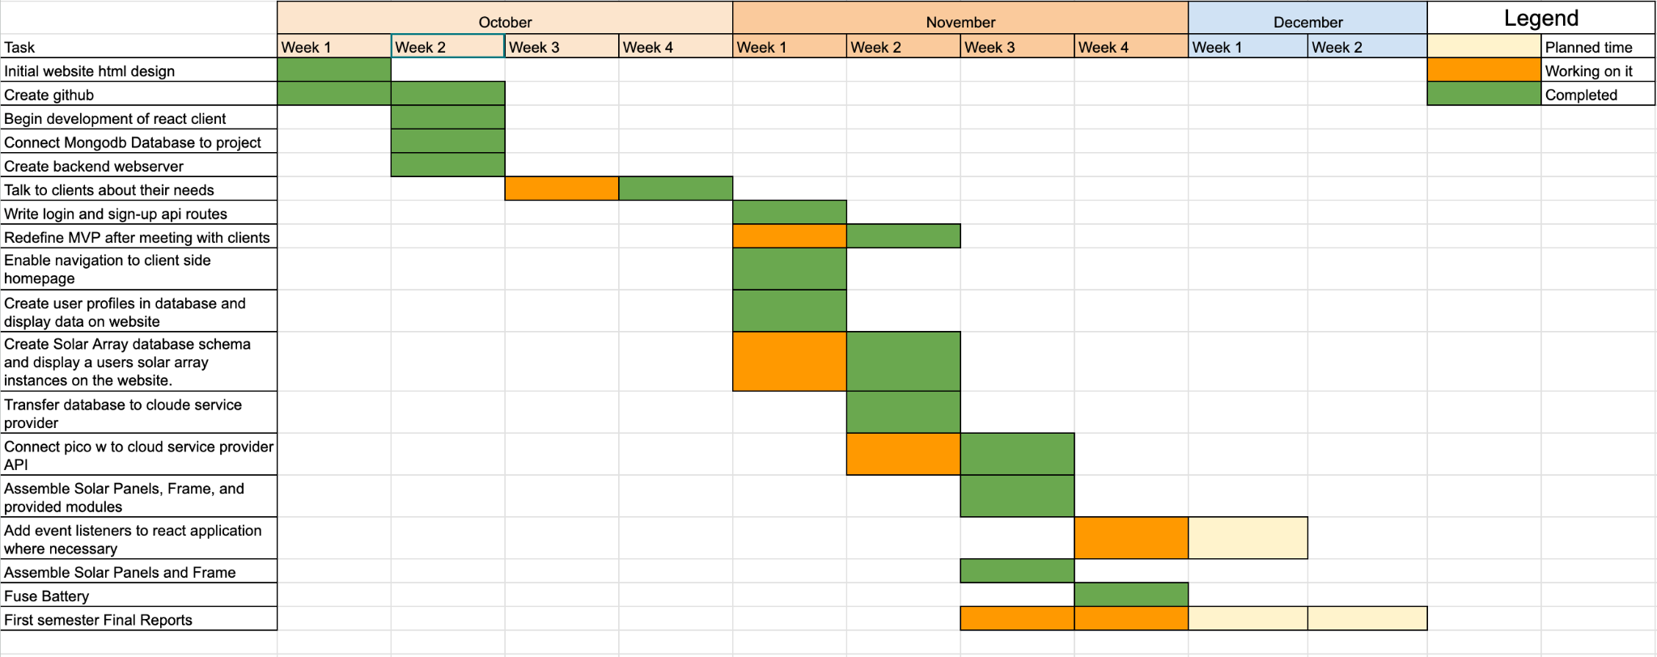
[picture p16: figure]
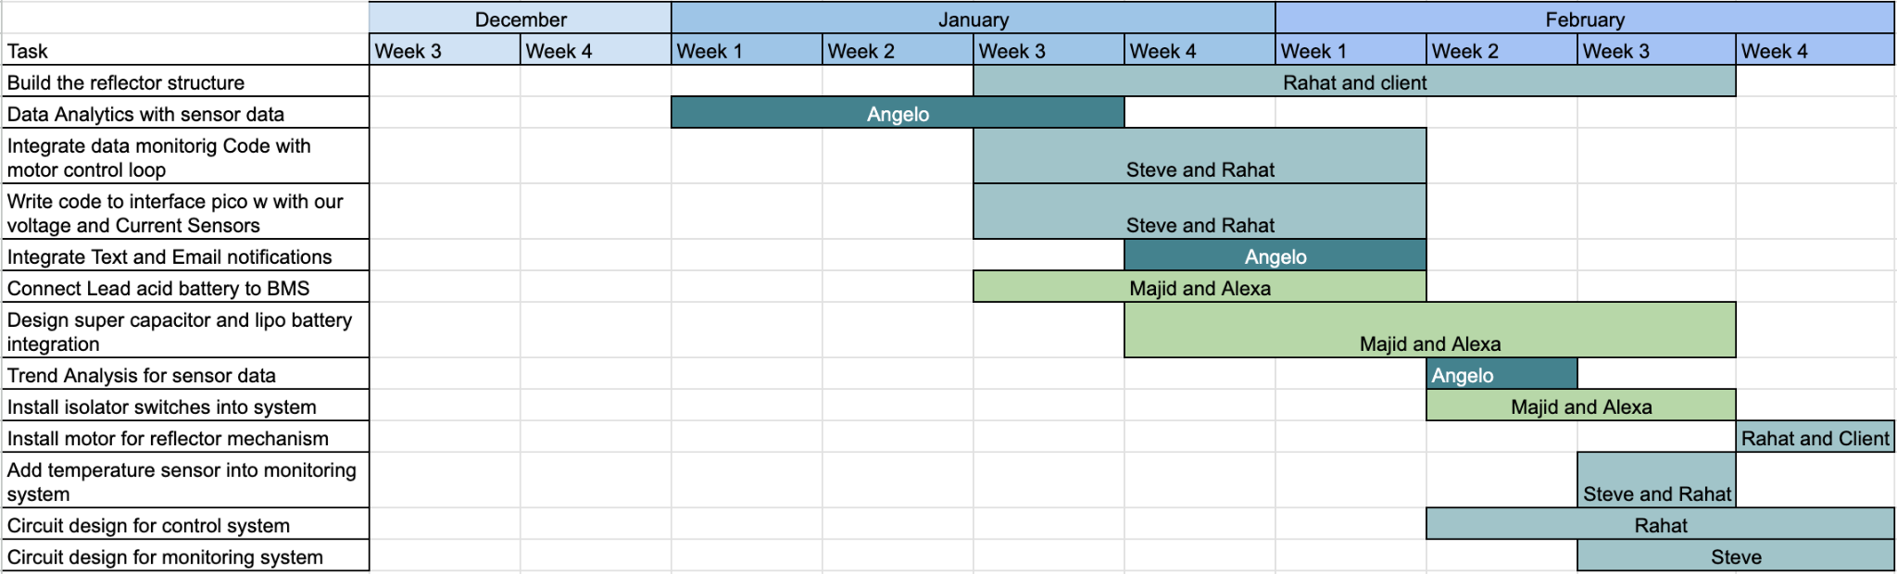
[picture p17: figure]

# 7.3 Appendix 3 – Other Appendices

Monitoring system :

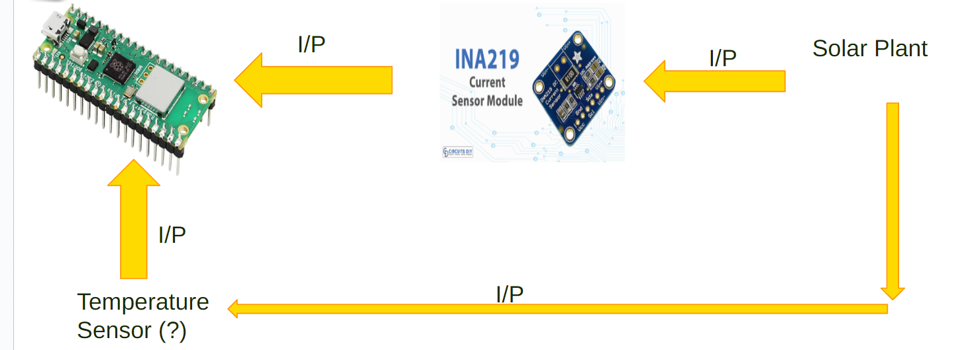
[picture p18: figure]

Figure : Block Diagram of Monitoring system

INA219 Sensor : The INA219 is a compact, I2C-compatible current shunt and power monitor. Key features include bi-directional current sensing, a voltage range from 0V to 26V, current range up to 3.2A, programmable calibration for varied current levels, and high accuracy in measurements. It supports standard and fast-mode I2C communications, making it easily integrable with microcontrollers like Raspberry Pi. This sensor is ideal for applications in energy monitoring, battery management, and power supply systems, where precise current and power measurement is essential.

Control System :

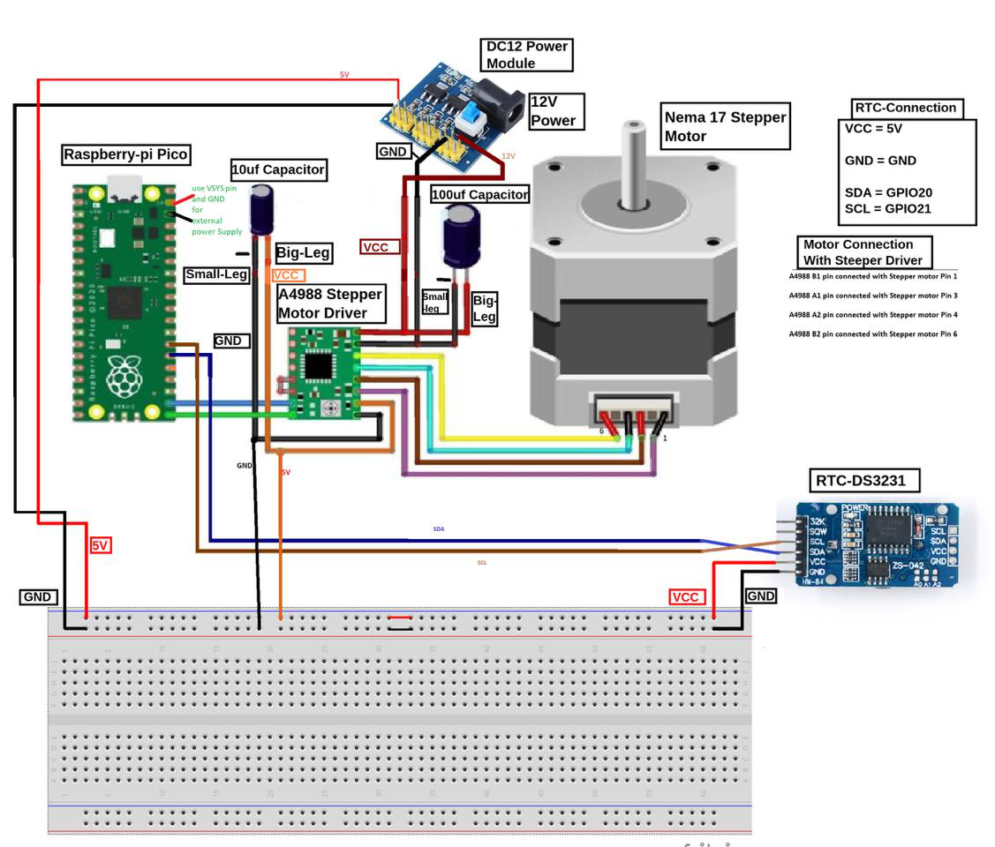
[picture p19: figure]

Figure : Wiring Diagram of the control system

RTC-DS3231: A precision Real Time Clock module with temperature compensation, I2C communication, and a backup battery feature for accurate timekeeping.

A4988 Stepper Motor Driver: A driver module for bipolar stepper motors, supporting up to 2A per coil and variable step sizes for precise motor control.

Nema 17 Stepper Motor: A standard-sized stepper motor known for its precision and high torque, commonly used in 3D printers and CNC machines.

Raspberry Pi Pico W: A microcontroller with Wi-Fi, based on the RP2040 chip, featuring dual-core processing, 264KB SRAM, and 2MB Flash memory, ideal for various applications and projects.

12V & 5V Power Supply: 12V power supply has been used for stepper motor driver and 5V for RTC module.

Solar Power Plant:

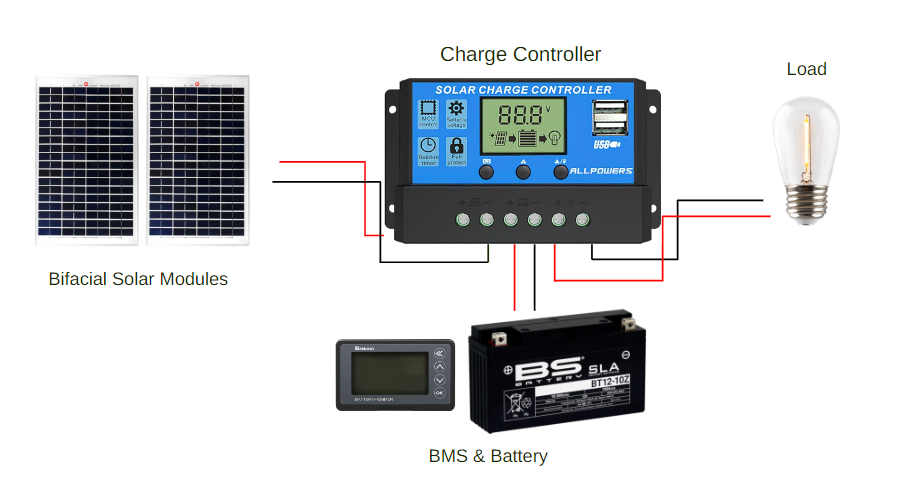
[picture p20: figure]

Figure : Block diagram of the Solar Power Plant

Bifacial Solar Panel (48V, 0.65A): Generates power through exposure to light. Model uses two single-faced photovoltaic panels wired in series, each generating 20W at peak output, for a total of 40W.

Charge Controller: Manages voltage and current from solar panels to protect the battery from overcharging or the load from drawing excess current.

12V SLA Battery: Features a reliable and low-maintenance Sealed Lead-Acid battery used for energy storage in solar systems.

BMS with Monitoring Display: Monitors and manages the battery's condition, ensuring safety and efficiency, equipped with a user-friendly display.

Small Light Bulb (Electrical Load): Demonstrates the practical use of stored solar energy for everyday electrical applications.

Figure 1. System Overview

Figure 2. Software Overview

Figure 3. UI

Team Information Sheet:

Rahat Mahmood is a senior undergraduate student at Boston University, majoring in Electrical Engineering. His industry experience includes designing Single Line Diagrams (SLD) and Three Line Diagrams (TLD) for 5-10 MW grid solar interconnection projects and involved in extracting and analyzing data from relevant studies for those projects. He has also been involved in conducting very high-level relay settings for transformers and Arc Flash calculations for renewable energy firms and utilities. Rahat is an active member of the IEEE Power and Energy Society and is committed to furthering his expertise in this area. He can be contacted at 857-389-5964 or rahat73@bu.edu

Steven Cheng is a senior Electrical Engineering student at Boston University. He has worked as a research assistant for Professor Joshua Semeter on data analysis of ionospheric data. Currently, he is an intern with Neural Dynamics Technologies as an embedded engineer. After graduation, Steven plans on moving to New London, Connecticut to work as a Systems Engineer for propulsion systems at General Dynamics Electric Boat. He can be contacted at stcheng@bu.edu or 201-783-7390.

Alexa Wiencek is a senior undergraduate student majoring in Electrical Engineering at Boston University. They have worked as a Learning Assistant for Engineering Mechanics, including giving a guest lecture for the course, as well as having been a coordinator of the Artemis Project in the summer of 2022. They have worked for Boston University’s Electronics Design Facility as a student technician. Currently, they are the acting recording secretary for the Kappa Sigma chapter of IEEE-HKN. After completing their undergraduate degree, Alexa will continue their studies, working towards a MS in Electrical and Computer Engineering. They can be contacted at awiencek@bu.edu or 646-531-2139.

Angelo Soyannwo is an undergraduate student at Boston University studying electrical and electronics engineering. He has previous experience working as an intern at James Cubitt architects as well as First Class Group dLimited. He has plans to incorporate his own company after graduation and is currently on track to complete his degree in Fall of 2024. He can be contacted at seun@bu.edu or 929-888-3930.

Majid Almuhaideb is a senior undergraduate student at Boston University, majoring in Electrical Engineering. He previously worked as a Teaching Assistant for Electric Circuits. He previously worked as an intern in management consulting firm McKinsey & Co, and plans to return after graduation. Majid is set to graduate in Fall of 2024. He can be contacted at majidmuh@bu.edu

This team was assembled to complete the senior design project described in this progress report. We will spend two semesters researching and designing the monitoring and control system requested by our client

References:

Abdelhady, Suzan & Borello, D. & Tortora, Eileen. (2014). Design of a small scale stand-alone solar thermal co-generation plant for an isolated region in Egypt. Energy Conversion and Management. 88. 872-882. 10.1016/j.enconman.2014.08.066.

Ang, Benjamin, et al. EC464 Capstone Senior Design Project User’s Manual Sol-R Solar Panel Installation, Boston University Electrical &amp; Computer Engineering, 1 May 2023.

Capone, Zachary, et al. EC464 Capstone Senior Design Project User’s Manual ClearSol, Boston University Electrical &amp; Computer Engineering, 25 Mar. 2022.

Laura Cozzi et al, “For the first time in decades, the number of people without access to electricity is set to increase in 2022”, IEA.com, published on July 17th 2014, accessed on 1st October 2023,

https://www.iea.org/commentaries/for-the-first-time-in-decades-the-number-of-people-without-access-to-electricity-is-set-to-increase-in-2022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,the%20numbers%2020%20years%20ago.

Pioneer Electric Cooperative inc, “Line Extension Cost”, pioneerelectric.coop, accessed on 1st October 2023, https://pioneerelectric.coop/my-account/help/line-extension-cost/.

Samantha M. Kelly, “Lithium-ion battery fires are happening more often. Here's how to prevent them”, last updated on 9th March 2023, accessed on 7th October 2023, https://www.kcra.com/article/lithium-ion-battery-fires-how-to-prevent-them/43266541#.

Shahzad, Umair. (2015). The Need For Renewable Energy Sources.

"Raspberry Pi," Raspberry Pi Foundation, [Online]. Available: https://www.raspberrypi.com/for-home/. [Accessed: September 21, 2023].

Team 15 SOL 12/9/2023

Team 15 SOL

Project Proposal page

First Semester Final Report

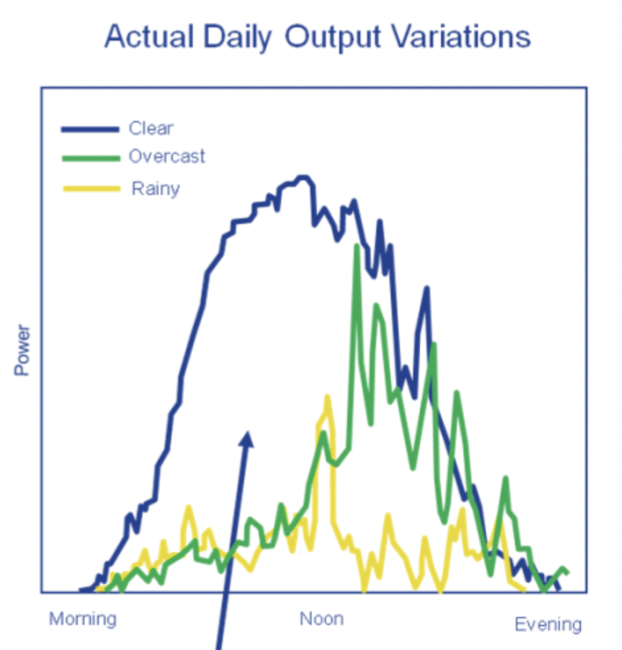
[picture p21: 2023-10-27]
Software/html_files/Assets/solar_graph.png

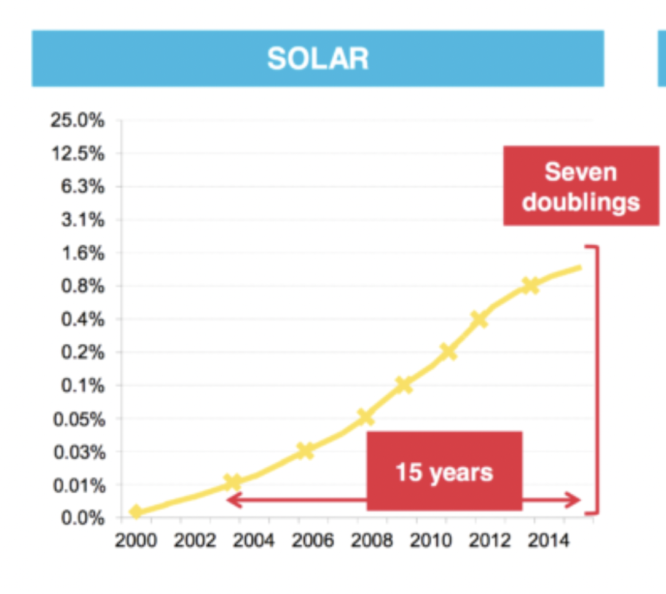
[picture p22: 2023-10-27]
Software/html_files/Assets/trend_graph.png

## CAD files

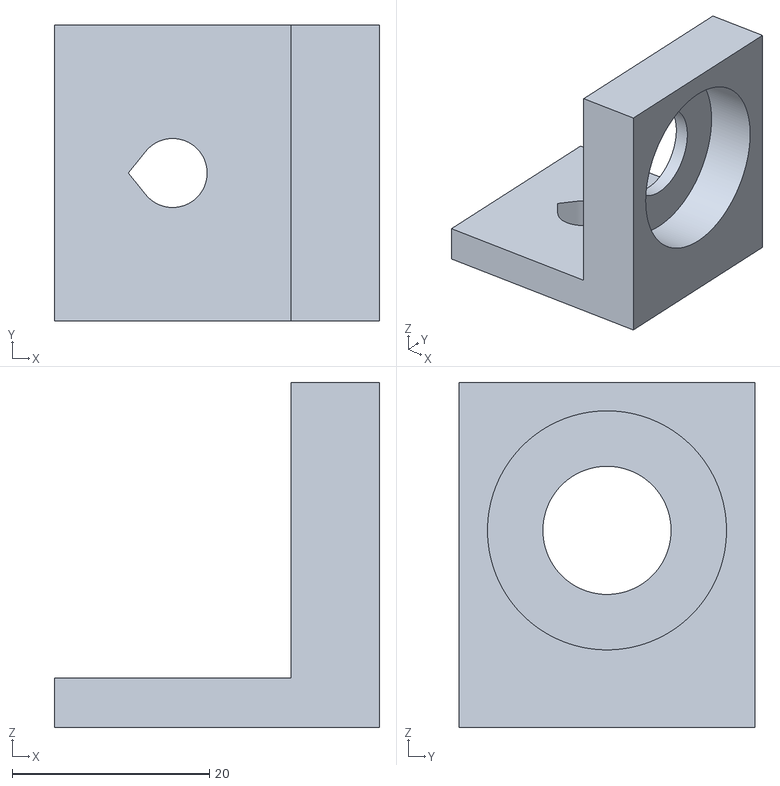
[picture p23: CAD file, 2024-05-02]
Hardware/STL/SOL - L Bracket.stl
33.0 x 30.0 x 35.0

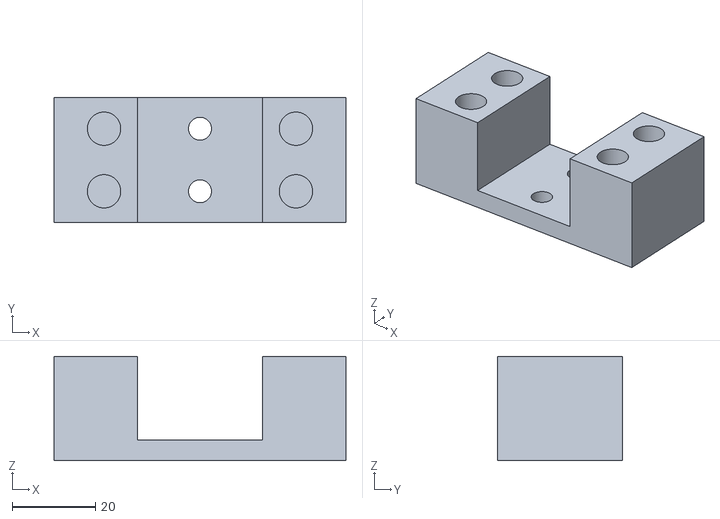
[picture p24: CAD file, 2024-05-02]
Hardware/STL/Rod Fastener v9.stl
70.0 x 30.0 x 25.0

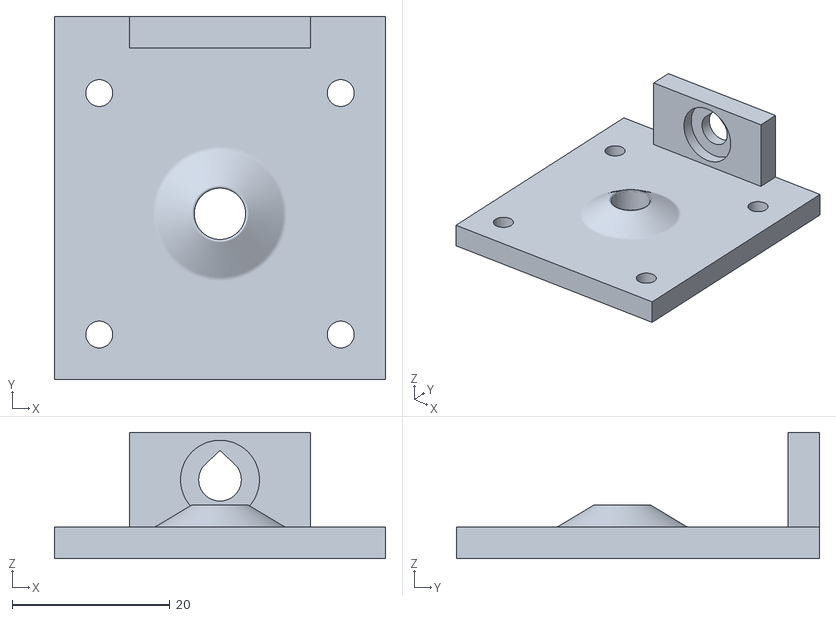
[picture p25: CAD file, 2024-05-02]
Hardware/STL/Motor Mount v16.stl
42.0 x 46.0 x 16.0

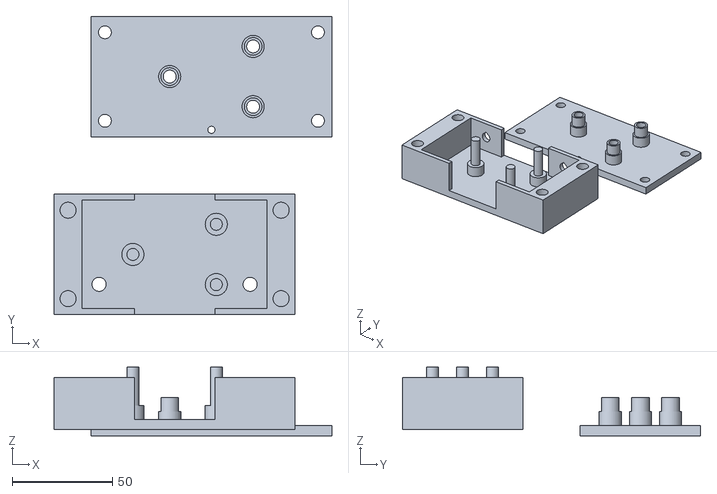
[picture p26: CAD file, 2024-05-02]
Hardware/STL/SOL - Faceplates.stl
138.3 x 148.5 x 34.1

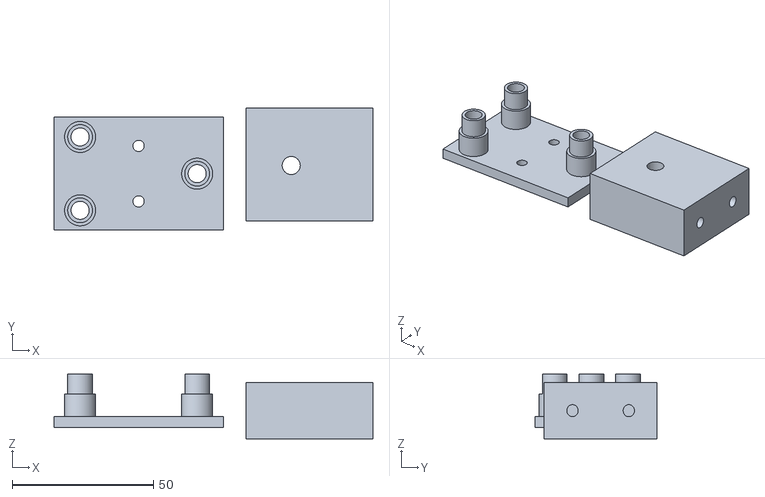
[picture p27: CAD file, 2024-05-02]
Hardware/STL/Bottom Plate v13.stl
113.1 x 43.3 x 23.0

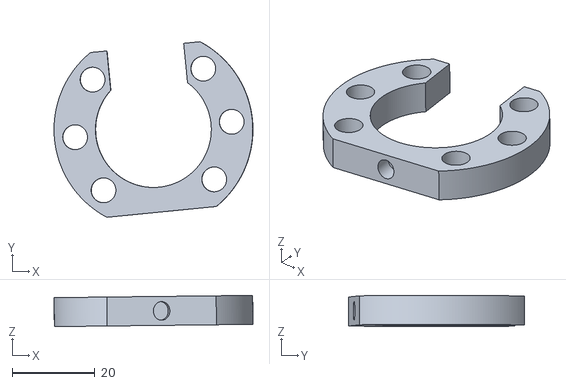
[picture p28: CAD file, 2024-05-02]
Hardware/STL/SOL - Screwlock.stl
48.1 x 42.4 x 7.54

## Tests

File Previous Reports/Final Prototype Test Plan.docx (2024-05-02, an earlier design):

Final Prototype Test Plan


Senior Design

ENG EC 463

To: Professor Pisano

From: Team 15

Team: Team 15

Date: 4/2/24

Subject: Final Prototype Testing Plan

1.0 Monitoring Circuit Data + Webserver Pairing
  1.1 Required Materials
    - Hardware
      - Light intensity sensor
      - 1 pico w microcontroller
      - Laptop to access webserver
      - USB to micro USB cord
      - Battery
    - Software
      - Backend express.js webserver
      - MongoDB database
      - React application
      - JavaScript functions
      - Micropython
  1.2 Pre-testing Setup Procedure
    - Connect system to power source
    - Open web server on laptop
  1.3 Testing Procedure
    - Live feed from our web server will show the readings of our BH175 light sensors.
    - A palm will be used to demonstrate our light sensor’s capabilities
  1.4 Measurable Criteria
    - Ability of webserver to display data collected in real-time
    - Wireless connection between control circuit and webserver
    - Professional display of data on webserver (Single graph will display solar irradiation)
2.0 Reflector Control System
  2.1 Required Materials
    - Reflector frame
    - Face plates, sliders, and connection bars
    - Stepper motor with ball screw
    - Reflector panels
  2.2 Set up
    - Reflector frame is fully assembled with sliding elements properly attached/ reflector panels have been attached at the rotating corner pieces of the face plates and lower bar sliders. The ball screw and stepper motor are attached to one side of the frame to move the reflectors up and down
  2.3 Pre-testing Setup Procedure
    - The team checks to ensure that all parts of the system are properly connected and that sliding parts move as intended/without resistance.
  2.4 Testing Procedure
    - Demonstrate the reflector panel’s range of motion
      - We will initialize the program and use the manual control buttons to demonstrate how to reset the reflector position when necessary
      - Then the system will run its demonstration program, which moves the reflectors more frequently than they would during the course of a day to better show system functionality in a short period of time
  2.5 Measurable Criteria
    - Reflectors moving smoothly in synch
    - the panels direct light towards the solar panels

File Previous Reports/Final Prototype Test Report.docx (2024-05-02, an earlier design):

Final Prototype Test Report


Senior Design

ENG EC 463

To: Professor Pisano

From: Team 15

Team: Team 15

Date: 4/18/24

Subject: Final Prototype Test Report

1.0 Reflector Control System + Webserver Pairing
  1.1 Set up
    - Reflector frame is fully assembled with sliding elements properly attached/ reflector panels have been attached at the rotating corner pieces of the face plates and lower bar sliders. The ball screw and stepper motor are attached to both sides of the frame to move the reflectors up and down.
    - The control system (including soldered/prepared PCB) is connected to the reflector system, allowing light sensor output to be sent to our web application.
    - We confirmed the reflector control system code is properly uploaded to the pico w being used for the test.
  1.2 Pre-testing Setup Procedure
    - The team checks to ensure that all parts of the system are properly connected and that sliding parts move as intended/without resistance.
    - We experienced a delay in our system functioning while setting up for today’s testing, but it was remedied before beginning our demonstration.
  1.3 Testing Procedure
    - We initialized the program and then ran the demonstration program, which moves the reflectors incrementally as our system searches for the optimal position. It does this by averaging the output from our two light sensors, and moves towards the direction in which it determines a greater total of received light. In a static environment, like the senior design lab, this results in the reflectors moving all the way up and down cyclically through their full range of motion.
  1.4 Measurable Criteria
    - Reflectors moving smoothly in synch
    - When hit, the limit switches cause the system to stop and reverse directions
    - The system visibly responds to change in light measured by the BH1750 sensors
2.0 Conclusion

We have put together a functioning proof of concept for our client as requested. Our prototype system demonstrates the functionality of this solar panel configuration, namely the use of reflectors to direct additional light to the panels. While there is still some improvement and polishing to be done in preparation for ECE Day, we have successfully demonstrated a functional prototype with a full range of reflector movement. Combined with our robust web application, we have done our part to advance the state of our client’s research endeavor. We have prepared his main team and any future senior design teams brought onboard to make continued advances as we have given them something to truly build off of.

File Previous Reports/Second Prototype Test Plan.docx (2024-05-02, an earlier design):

Second Prototype Test Plan


Senior Design

ENG EC 463

To: Professor Pisano

From: Team 15

Team: Team 15

Date: 2/27/24

Subject: Second Prototype Testing Plan

1.0 Monitoring Circuit Data + Webserver Pairing
  1.1 Required Materials
    - Hardware
      - Light intensity sensor
      - Temperature sensor
      - Voltage/current sensor
      - 2 pico w microcontrollers
      - Laptop to access webserver
      - Solar charge controller
      - Battery
      - USB to microUSB cord
      - Lamp (external light source)
    - Software
      - Backend express.js webserver
      - MongoDB database
      - React application
      - JavaScript functions
      - Micropython
  1.2 Set up
    - Each half of the monitoring circuit has been paired with the web server.
  1.3 Pre-testing Setup Procedure
    - Have the monitoring circuit laid out
    - Connect to battery for power via 5V source on solar charge controller
    - Open webserver on laptop
  1.4 Testing Procedure
    - Live feed from our web server will show the readings of our various sensors.
    - A small lamp will be used as an external light source to demonstrate our light sensor’s capabilities
  1.5 Measurable Criteria
    - Ability of webserver to display data collected in real time
    - Wireless connection between monitoring circuit(s) and webserver
    - Professional display of data on webserver

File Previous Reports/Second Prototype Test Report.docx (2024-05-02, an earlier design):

Second Prototype Test Plan


Senior Design

ENG EC 463

To: Professor Pisano

From: Team 15

Team: Team 15

Date: 3/6/24

Subject: Second Prototype Test Report

1.0 Monitoring Circuit Data + Webserver Pairing (Hardware/Software Integration)
  1.1 Set up

The monitoring circuit is laid out. The microcontrollers had been prepared with the code uploaded and had been paired with the web server to wirelessly transmit data. For the prototype, the circuit elements are connected over two small breadboards, but the final product will utilize a PCB.

  1.2 Pre-testing Setup Procedure
    - Have the monitoring circuit laid out
    - Connect to battery for power via 5V source on solar charge controller
    - Open webserver on laptop
  1.3 Testing Procedure
    - Live feed from our web server shows the readings/graphs of our various sensors
    - A small lamp was used as an external light source to demonstrate our light sensor’s capabilities
    - The circuit was connected to the benchtop oscilloscope to demonstrate that the figures from our webserver display are accurate
  1.4 Measurable Criteria
    - Ability of webserver to display data collected in real time
    - Wireless connection between monitoring circuit(s) and webserver
    - Professional display of data on webserver
2.0 Conclusion

This test was successful as we successfully integrated the two main components of our project, the physical monitoring circuit and our cloud database/webserver UI. We have verified that the data obtained wirelessly is accurate by probing key points in the circuit, and the UI of our webserver to display these values includes rather polished graphs. The fact that the server is now ready to take, log, and display data from the solar panel set up means we are well on track to make additional progress. Our focus as a team can now shift to webserver UI for mobile browsers, the control circuit, designing/ordering a PCB for the monitoring circuit, and finalize the parts for/assemble our solar panel frame and reflector setup.

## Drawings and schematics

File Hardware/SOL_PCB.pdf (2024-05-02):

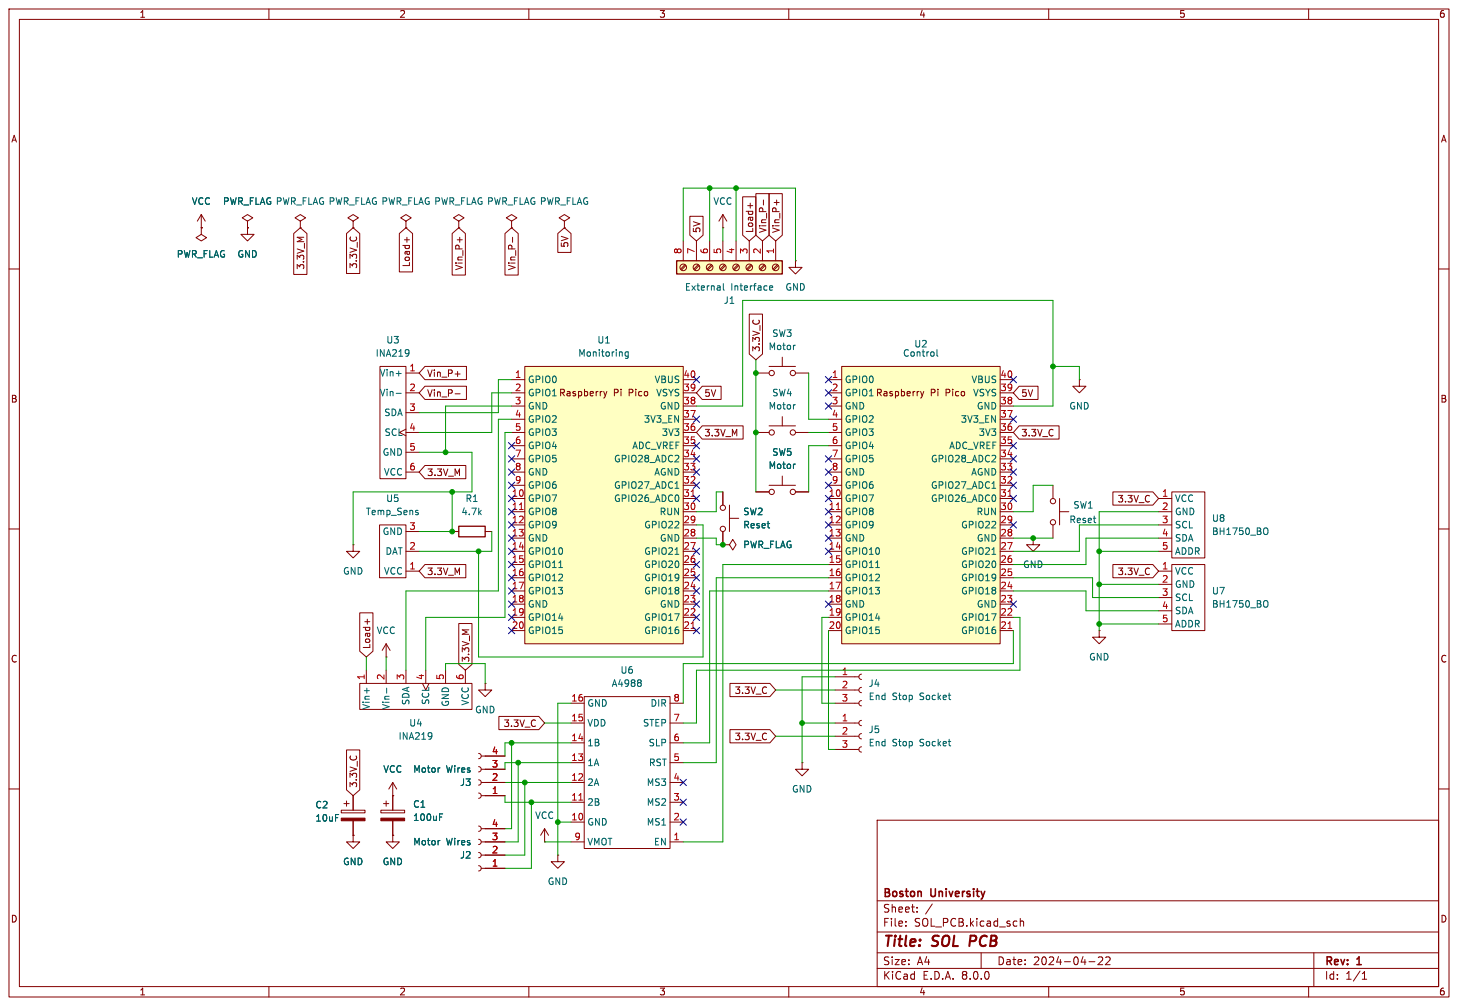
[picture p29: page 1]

1 Vin- 2 SDA
J3 Motor Wires GND Vin+

File: SOL_PCB.kicad_sch Sheet: / Boston University GND

Id: 1/1 Title: SOL PCB

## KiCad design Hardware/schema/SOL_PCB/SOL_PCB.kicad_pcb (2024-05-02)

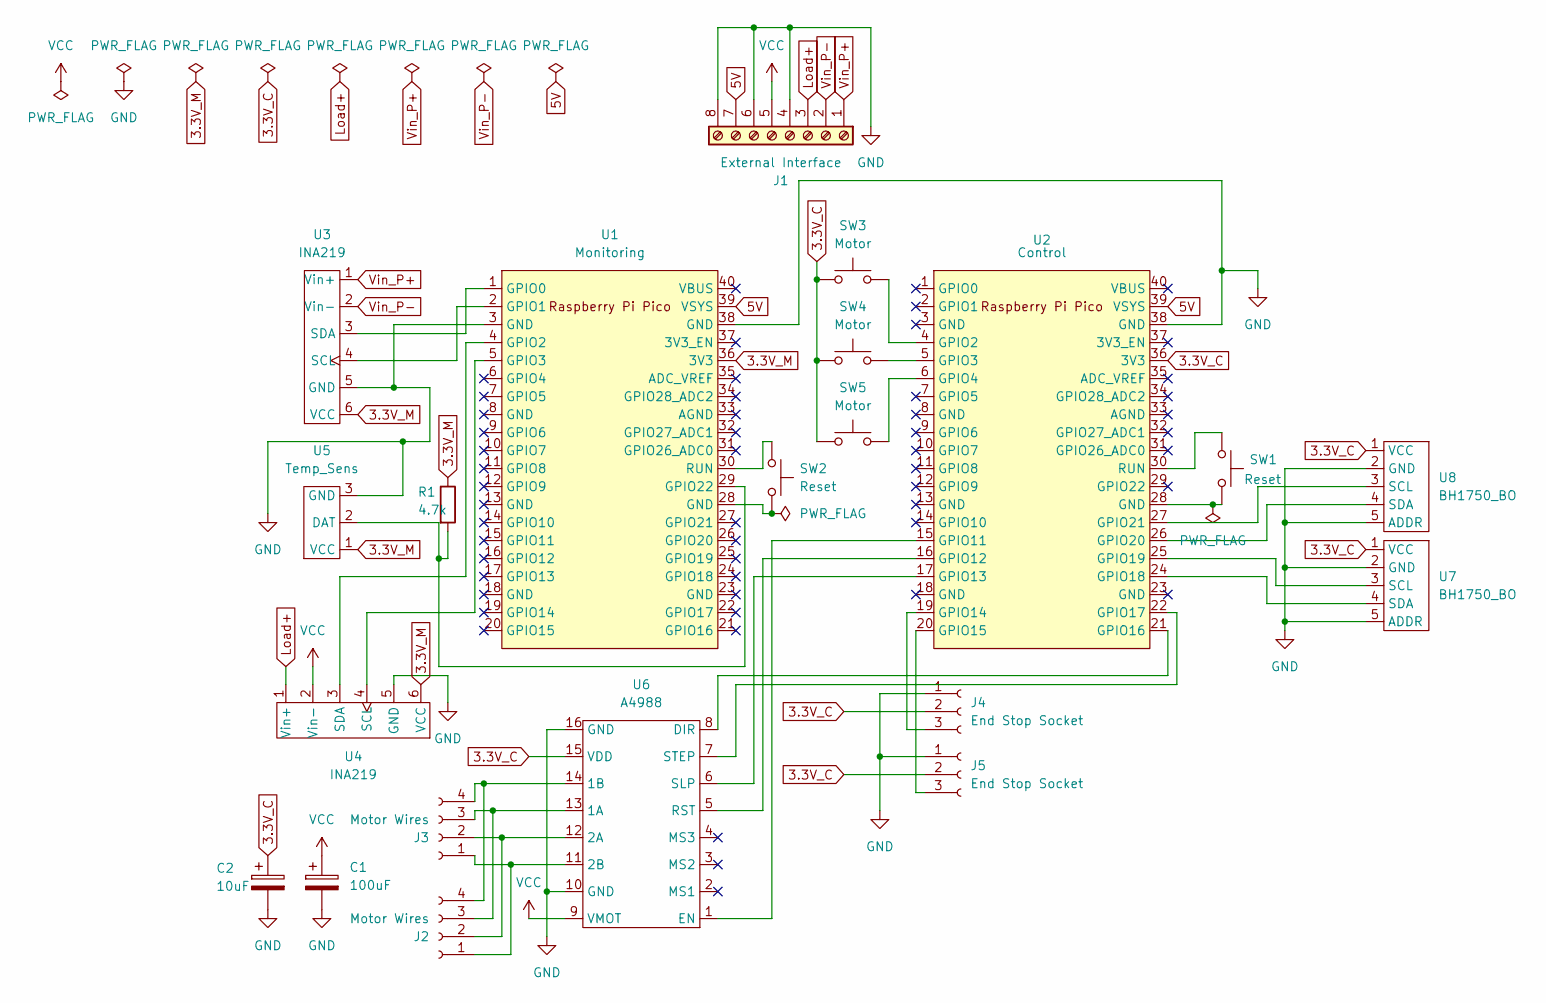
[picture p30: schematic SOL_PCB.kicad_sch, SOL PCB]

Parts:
C1: 100uF; CP_Radial_D6.3mm_P2.50mm
C2: 10uF; CP_Radial_D5.0mm_P2.50mm
J1: External Interface; TerminalBlock_Phoenix_MKDS-1,5-8_1x08_P5.00mm_Horizontal
J2, J3: Motor Wires; PinSocket_1x04_P2.54mm_Vertical
J4, J5: End Stop Socket; PinSocket_1x03_P2.54mm_Vertical
R1: 4.7k; R_Axial_DIN0207_L6.3mm_D2.5mm_P15.24mm_Horizontal
SW1, SW2: Reset; SW_PUSH_6mm_H4.3mm
SW3, SW4, SW5: Motor; SW_PUSH_6mm_H4.3mm
U1: Monitoring; RPi_Pico_SMD_TH
U2: Control; RPi_Pico_SMD_TH
U3, U4: INA219; INA219_Breakout
U5: Temp_Sens; Temp_Sensor
U6: A4988; A4988 Driver
U7, U8: BH1750_BO; BH1750

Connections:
3.3V_C: C2.1, J4.2, J5.2, SW3.1, SW4.1, SW5.1, U2.36 (3V3), U6.15 (VDD), U7.1 (VCC), U8.1 (VCC)
3.3V_M: R1.1, U1.36 (3V3), U3.6 (VCC), U4.6 (VCC), U5.1 (VCC)
5V: J1.7, U1.39 (VSYS), U2.39 (VSYS)
GND: C1.2, C2.2, J1.4, J1.6, J1.8, J4.1, J5.1, U1.3 (GND), U1.38 (GND), U2.38 (GND), U3.5 (GND), U4.5 (GND), U5.3 (GND), U6.10 (GND), U6.16 (GND), U7.2 (GND), U7.5 (ADDR), U8.2 (GND), U8.5 (ADDR)
Load+: J1.3, U4.1 (Vin+)
unnamed: J2.1, J3.1, U6.11 (2B)
unnamed: J2.2, J3.2, U6.12 (2A)
unnamed: J2.3, J3.3, U6.13 (1A)
unnamed: J2.4, J3.4, U6.14 (1B)
unnamed: J4.3, U2.19 (GPIO14)
unnamed: J5.3, U2.20 (GPIO15)
unnamed: SW1.2, U2.28 (GND)
unnamed: SW2.2, U1.28 (GND)
unnamed: U1.1 (GPIO0), U3.3 (SDA)
unnamed: U1.2 (GPIO1), U3.4 (SCL)
unnamed: U1.4 (GPIO2), U4.3 (SDA)
unnamed: U1.5 (GPIO3), U4.4 (SCL)
unnamed: R1.2, U1.29 (GPIO22), U5.2 (DAT)
unnamed: SW2.1, U1.30 (RUN)
unnamed: SW3.2, U2.4 (GPIO2)
unnamed: SW4.2, U2.5 (GPIO3)
unnamed: SW5.2, U2.6 (GPIO4)
unnamed: U2.15 (GPIO11), U6.1 (EN)
unnamed: U2.16 (GPIO12), U6.5 (RST)
unnamed: U2.17 (GPIO13), U6.6 (SLP)
unnamed: U2.21 (GPIO16), U6.8 (DIR)
unnamed: U2.22 (GPIO17), U6.7 (STEP)
unnamed: U2.24 (GPIO18), U7.4 (SDA)
unnamed: U2.25 (GPIO19), U7.3 (SCL)
unnamed: U2.26 (GPIO20), U8.4 (SDA)
unnamed: U2.27 (GPIO21), U8.3 (SCL)
unnamed: SW1.1, U2.30 (RUN)
VCC: C1.1, J1.5, U4.2 (Vin-), U6.9 (VMOT)
Vin_P+: J1.1, U3.1 (Vin+)
Vin_P-: J1.2, U3.2 (Vin-)

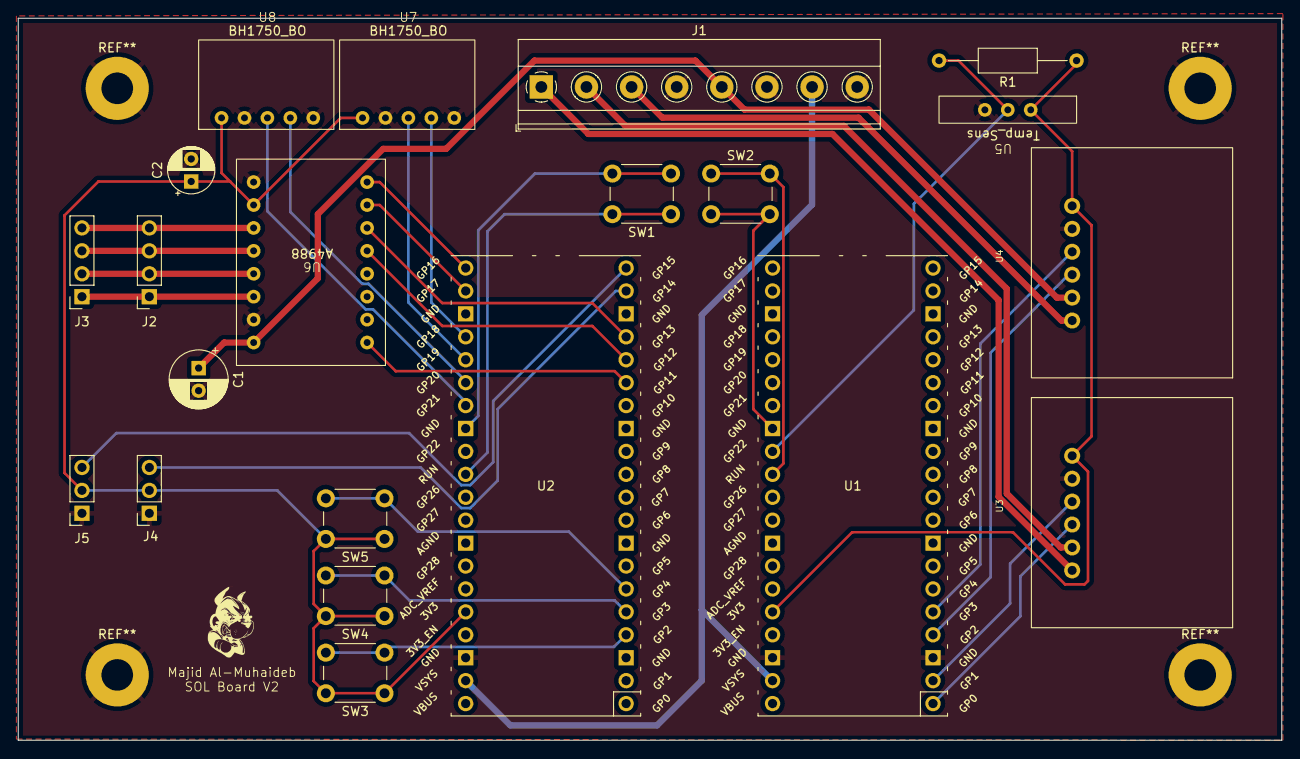
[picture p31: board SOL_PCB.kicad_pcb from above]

Board: 2 copper layers, 140.0 x 80.0 mm, 21 parts (0 on the bottom side), 35 nets.

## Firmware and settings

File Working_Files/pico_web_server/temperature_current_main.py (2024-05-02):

# Import necessary libraries
import machine, utime, onewire, ds18x20
from ina219 import INA219

import json
import network
import urequests as requests
import time
import machine

import umail

# Internal libs
#import constants


#from bh1750 import BH1750

# Initialize I2C for INA219 and BH1750
i2c_ina219 = machine.I2C(0, scl=machine.Pin(1), sda=machine.Pin(0))
#i2c_bh1750 = machine.I2C(0, scl=machine.Pin(21), sda=machine.Pin(20))  # Adjust pins as necessary

# INA219 sensor setup
sensor_ina219 = INA219(i2c_ina219, 0x40)

# BH1750 light sensor setup
#sensor_bh1750 = BH1750(i2c_bh1750, 0x23)

# Function to calculate actual voltage considering the voltage divider
def actual_voltage(measured_voltage):
    # divider_ratio = 4.67 / (5.6+4.67)  # R2 / (R2+R1), use when necessary
    return measured_voltage

url = "https://us-east-1.aws.data.mongodb-api.com/app/data-frxlp/endpoint/data/v1/action/"

def connect_to_wifi(ssid, psk):
    wlan = network.WLAN(network.STA_IF)
    wlan.active(True)
    wlan.connect(ssid, psk)

    while not wlan.isconnected() and wlan.status() >= 0:
        print("Waiting to Connect")
        time.sleep(10)
    if not wlan.isconnected():
        raise Exception("Wifi not available")
    print("Connected to WiFi")

def createOne(date):
    try:
        headers = {
            "api-key": "fuQa5n8PAJ38cvm0m1kAjfCuI3slNoBpPHYud7uTR2RsIeY75F8RcGGSAUGjPWXB",
            #"Connection": "upgrade",
            #"Upgrade": "HTTP/2.0, SHTTP/1.3, IRC/6.9, RTA/x11"
        }
        filter_dict = {"day": date}
        document = {"day": date, "temperature_farenheit": [], "luminances": [], "temperature_celcius": [], "times": []}
        update = {"$set": document}
        searchPayload = {
            "dataSource": "Sol-Cluster",
            "database": "Sol",
            "collection": "graphs",
            "filter": filter_dict,
            "update": document,
            "upsert": True,
        }
        response = requests.post(url + "updateOne", headers=headers, json=searchPayload)
        print("Response: (" + str(response.status_code) + "), msg = " + str(response.text))
        if response.status_code >= 200 and response.status_code < 300:
            print("Success Response")
            print("graph created")
            
        else:
            print(response.status_code)
            print("Error")
        response.close()
    except Exception as e:
        print(e)


def findOne(filter_dict):
    try:
        headers = {
            "api-key": "fuQa5n8PAJ38cvm0m1kAjfCuI3slNoBpPHYud7uTR2RsIeY75F8RcGGSAUGjPWXB",
            #"Connection": "upgrade",
            #"Upgrade": "HTTP/2.0, SHTTP/1.3, IRC/6.9, RTA/x11"
        }
        searchPayload = {
            "dataSource": "Sol-Cluster",
            "database": "Sol",
            "collection": "graphs",
            "filter": filter_dict,
            #"update": update_dict,
            #"upsert": True,
        }
        response = requests.post(url + "findOne", headers=headers, json=searchPayload)
        print("Response: (" + str(response.status_code) + "), msg = " + str(response.text))
        if response.status_code >= 200 and response.status_code < 300:
            if response.text == "{\"document\":null}":
                print("No graph corresponding to todays date found")
                print(filter_dict["day"])
                createOne(filter_dict["day"])
                
        else:
            print(response.status_code)
            print("findOne Error")
        response.close()
    except Exception as e:
        print(e)

def updateOne(filter_dict, update_dict):
    try:
        headers = {
            "api-key": "fuQa5n8PAJ38cvm0m1kAjfCuI3slNoBpPHYud7uTR2RsIeY75F8RcGGSAUGjPWXB",
            #"Connection": "upgrade",
            #"Upgrade": "HTTP/2.0, SHTTP/1.3, IRC/6.9, RTA/x11"
        }
        update = {"$set": update_dict}
        searchPayload = {
            "dataSource": "Sol-Cluster",
            "database": "Sol",
            "collection": "temperatures",
            "filter": filter_dict,
            "update": update_dict,
            "upsert": True,
        }
        response = requests.post(url + "updateOne", headers=headers, json=searchPayload)
        print("Response: (" + str(response.status_code) + "), msg = " + str(response.text))
        if response.status_code >= 200 and response.status_code < 300:
            print("Success Response")
            
        else:
            print(response.status_code)
            print("Error")
        response.close()
    except Exception as e:
        print(e)

def pushOne(filter_dict, update_dict):
    try:
        headers = {
            "api-key": "fuQa5n8PAJ38cvm0m1kAjfCuI3slNoBpPHYud7uTR2RsIeY75F8RcGGSAUGjPWXB",
            #"Connection": "upgrade",
            #"Upgrade": "HTTP/2.0, SHTTP/1.3, IRC/6.9, RTA/x11"
        }
        update = {"$push": update_dict}
        searchPayload = {
            "dataSource": "Sol-Cluster",
            "database": "Sol",
            "collection": "graphs",
            "filter": filter_dict,
            "update": update,
            #"upsert": True,
        }
        response = requests.post(url + "updateOne", headers=headers, json=searchPayload)
        print("Response: (" + str(response.status_code) + "), msg = " + str(response.text))
        if response.status_code >= 200 and response.status_code < 300:
            print("Success Response")
            
        else:
            print(response.status_code)
            print("Error")
        response.close()
    except Exception as e:
        print(e)
        
#Functions to update the days collection in the database
def createOneDay(date):
    try:
        headers = {
            "api-key": "fuQa5n8PAJ38cvm0m1kAjfCuI3slNoBpPHYud7uTR2RsIeY75F8RcGGSAUGjPWXB",
            #"Connection": "upgrade",
            #"Upgrade": "HTTP/2.0, SHTTP/1.3, IRC/6.9, RTA/x11"
        }
        filter_dict = {"day": date}
        document = {"times": [], "power": [], "date": date,}
        update = {"$set": document}
        searchPayload = {
            "dataSource": "Sol-Cluster",
            "database": "Sol",
            "collection": "days",
            "filter": filter_dict,
            "update": document,
            "upsert": True,
        }
        response = requests.post(url + "updateOne", headers=headers, json=searchPayload)
        print("Response: (" + str(response.status_code) + "), msg = " + str(response.text))
        if response.status_code >= 200 and response.status_code < 300:
            print("Success Response")
            print("day created")
            
        else:
            print(response.status_code)
            print("Error")
        response.close()
    except Exception as e:
        print(e)


def findOneDay(filter_dict):
    try:
        headers = {
            "api-key": "fuQa5n8PAJ38cvm0m1kAjfCuI3slNoBpPHYud7uTR2RsIeY75F8RcGGSAUGjPWXB",
            #"Connection": "upgrade",
            #"Upgrade": "HTTP/2.0, SHTTP/1.3, IRC/6.9, RTA/x11"
        }
        searchPayload = {
            "dataSource": "Sol-Cluster",
            "database": "Sol",
            "collection": "days",
            "filter": filter_dict,
            #"update": update_dict,
            #"upsert": True,
        }
        response = requests.post(url + "findOne", headers=headers, json=searchPayload)
        print("Response: (" + str(response.status_code) + "), msg = " + str(response.text))
        if response.status_code >= 200 and response.status_code < 300:
            if response.text == "{\"document\":null}":
                print("No day corresponding to todays date found")
                print(filter_dict["date"])
                createOneDay(filter_dict["date"])
                
        else:
            print(response.status_code)
            print("findOne Error")
        response.close()
    except Exception as e:
        print(e)


def pushOneDay(filter_dict, update_dict):
    try:
        headers = {
            "api-key": "fuQa5n8PAJ38cvm0m1kAjfCuI3slNoBpPHYud7uTR2RsIeY75F8RcGGSAUGjPWXB",
            #"Connection": "upgrade",
            #"Upgrade": "HTTP/2.0, SHTTP/1.3, IRC/6.9, RTA/x11"
        }
        update = {"$push": update_dict}
        searchPayload = {
            "dataSource": "Sol-Cluster",
            "database": "Sol",
            "collection": "days",
            "filter": filter_dict,
            "update": update,
            #"upsert": True,
        }
        response = requests.post(url + "updateOne", headers=headers, json=searchPayload)
        print("Response: (" + str(response.status_code) + "), msg = " + str(response.text))
        if response.status_code >= 200 and response.status_code < 300:
            print("Success Response")
            
        else:
            print(response.status_code)
            print("Error")
        response.close()
    except Exception as e:
        print(e)
        
def updateCurrentAndVoltage(filter_dict, update_dict):
    try:
        headers = {
            "api-key": "fuQa5n8PAJ38cvm0m1kAjfCuI3slNoBpPHYud7uTR2RsIeY75F8RcGGSAUGjPWXB",
            #"Connection": "upgrade",
            #"Upgrade": "HTTP/2.0, SHTTP/1.3, IRC/6.9, RTA/x11"
        }
        update = {"$set": update_dict}
        searchPayload = {
            "dataSource": "Sol-Cluster",
            "database": "Sol",
            "collection": "solararrays",
            "filter": filter_dict,
            "update": update_dict,
            "upsert": True,
        }
        response = requests.post(url + "updateOne", headers=headers, json=searchPayload)
        print("Response: (" + str(response.status_code) + "), msg = " + str(response.text))
        if response.status_code >= 200 and response.status_code < 300:
            print("Success Response")
            
        else:
            print(response.status_code)
            print("Error")
        response.close()
    except Exception as e:
        print(e)
        
def insertAnomaly(filter_dict, update_dict):
    try:
        headers = {
            "api-key": "fuQa5n8PAJ38cvm0m1kAjfCuI3slNoBpPHYud7uTR2RsIeY75F8RcGGSAUGjPWXB",
            #"Connection": "upgrade",
            #"Upgrade": "HTTP/2.0, SHTTP/1.3, IRC/6.9, RTA/x11"
        }
        update = {"$set": update_dict}
        searchPayload = {
            "dataSource": "Sol-Cluster",
            "database": "Sol",
            "collection": "anomalies",
            "filter": filter_dict,
            "update": update_dict,
            "upsert": True,
        }
        response = requests.post(url + "updateOne", headers=headers, json=searchPayload)
        print("Response: (" + str(response.status_code) + "), msg = " + str(response.text))
        if response.status_code >= 200 and response.status_code < 300:
            print("Success Response")
            
        else:
            print(response.status_code)
            print("Error")
        response.close()
    except Exception as e:
        print(e)
        
def findSolarArrayEmailList(filter_dict):
    try:
        headers = {
            "api-key": "fuQa5n8PAJ38cvm0m1kAjfCuI3slNoBpPHYud7uTR2RsIeY75F8RcGGSAUGjPWXB",
            #"Connection": "upgrade",
            #"Upgrade": "HTTP/2.0, SHTTP/1.3, IRC/6.9, RTA/x11"
        }
        searchPayload = {
            "dataSource": "Sol-Cluster",
            "database": "Sol",
            "collection": "solararrays",
            "filter": filter_dict,
            #"update": update_dict,
            #"upsert": True,
        }
        response = requests.post(url + "findOne", headers=headers, json=searchPayload)
        print("Response: (" + str(response.status_code) + "), msg = " + str(response.text))
        if response.status_code >= 200 and response.status_code < 300:
            if response.text == "{\"document\":null}":
                print("No Solar Array found")
                return []
            else:
                print(response.json()["document"]["email_list"])
                return response.json()["document"]["email_list"]
               
                
        else:
            print(response.status_code)
            print("findOne Error")
        response.close()
    except Exception as e:
        print(e)

def main():
    
    # Initialize DS18B20 temperature sensor
    ds_pin = machine.Pin(22)
    ds_sensor = ds18x20.DS18X20(onewire.OneWire(ds_pin))
    roms = ds_sensor.scan()
    
    connect_to_wifi("BU Guest (unencrypted)", "")
    
    while True:
        try:
            
            response = requests.get(url='http://worldtimeapi.org/api/timezone/America/New_York')
            date=response.json()["datetime"][0:10].replace("-", "/")
            
            print(response.json()["datetime"])
            
            power = 0
            voltage_reading = 0
            current_reading = 0
            
            try:
                measured_voltage = sensor_ina219.getBusVoltage_V()  # Bus Voltage in volts
                current = sensor_ina219.getCurrent_mA()  # Current in milliamps # Connect Vin of INA219 to the + of load
                real_current = current/1000
                adjusted_voltage = actual_voltage(measured_voltage)  # Adjusted voltage in volts
                power = (adjusted_voltage * real_current)/1000 # power in wats
                voltage_reading = adjusted_voltage
                current_reading = real_current
                print(f"Adjusted Voltage: {adjusted_voltage:.2f} V, Current: {real_current:.2f} mA")
                
            except Exception as e:
                
                print("INA219 read error:", e)
                
            ds_sensor.convert_temp()
            utime.sleep_ms(750)  # Wait for DS18B20 conversion
            tempC = 0
            tempF = 0
            for rom in roms:
                tempC = ds_sensor.read_temp(rom)
                tempF = tempC * (9/5) + 32
                print(f"DS18B20 Temperature (ºC): {tempC:.2f}, Temperature (ºF): {tempF:.2f}")
            

            print(tempC)
            print(tempF)
            print(power)
            
            # graph filter dict
            filterDict = {
                    "day": date,
            }
            
            #print("sending...")
            
            #update graph (temperature, luminosity and timestamps)
            findOne(filterDict)
            print("Updating temperature, luminosity")
            pushOne(filterDict, {"temperature_farenheit": tempF})
            pushOne(filterDict, {"times": response.json()["datetime"]})
            pushOne(filterDict, {"temperature_celsius": tempC})
            updateOne({"day": "current_day"}, {"day": "current_day", "temperature_celsius": tempC, "temperature_farenheit": tempF})
            
            #Update the day with power and and timestamp data
            findOneDay({"date": date})
            print("Updating power")
            pushOneDay({"date": date}, {"power": power})
            pushOneDay({"date": date}, {"times": response.json()["datetime"][0:-4] + '0:00'})
            
            email_list = findSolarArrayEmailList({"id": "65539e775435e37264e3e6ff"})
            
            if (current_reading < 0.1 or voltage_reading < 0.1):
                # Email details
                sender_email = "angelosoyannwo@gmail.com"
                sender_name = "Team 15 Solar Power Module"
                sender_app_password = "xrju iocy danb cjkm"
                email_subject ='Solar Power Module Anomaly'
                
                for i in range(len(email_list)):
                    # Send the email
                    # Connect to the Gmail's SSL port
                    smtp = umail.SMTP('smtp.gmail.com', 465, ssl=True)
                    # Login to the email account using the app password
                    smtp.login(sender_email, sender_app_password)
                    # Specify the recipient email address
                    smtp.to(email_list[i])
                    # Write the email header
                    smtp.write("From:" + sender_name + "<"+ sender_email+">\n")
                    smtp.write("Subject:" + email_subject + "\n")
                    # Write the body of the email
                    text = f"An anomaly has occurred in the operation of the solar plant.\nVoltage: {voltage_reading:.2f} V, Current: {current_reading:.2f} mA"
                    smtp.write(text)
                    # Send the email
                    smtp.send()
                    # Quit the email session
                    smtp.quit()

                    print('Email Sent')
                
                
                
                insertAnomaly({"date": response.json()["datetime"][0:-4] + '0:00'},
                              
                              {"date": response.json()["datetime"][0:-4] + '0:00',
                               "current": current_reading,
                               "voltage": voltage_reading,
                               }
                              )
                
                
            
            
            #Update current and voltage values
            filter_dictionary = {"id": "65539e775435e37264e3e6ff"}
            
            update_dictionary = {"id": "65539e775435e37264e3e6ff",
                                 "Voltage_reading": str(voltage_reading),
                                 "location": "Warren Towers",
                                 "solarPanels": [],
                                 "Current_reading": str(current_reading),
                                 "email_list": email_list,
                                 }
            updateCurrentAndVoltage(filter_dictionary, update_dictionary)

            print("Finished updating")
            #updateOne(filterDict, updateDict)
             
            time.sleep(30)
                
        except Exception as e:
            print(e)

#readPower(1000)
if __name__ == "__main__":
    main()

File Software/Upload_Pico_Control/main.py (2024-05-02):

import time
from machine import Pin, RTC, I2C
from math import fabs, floor
# import uasyncio
# import queue
# from lux_sensor_main import i2c2, light_sensor2
from lux_sensor_main import luxMain, connect_to_wifi
#from bh1750 import BH1750
import bh1750
import limSwitch
import manualMotor
import globalVars

# Initialize light sensors
i2c1 = I2C(0, scl=Pin(21), sda=Pin(20))
i2c2 = I2C(1, scl=Pin(19), sda=Pin(18))
# Create an instance of the BH1750 class
light_sensor1 = bh1750.BH1750(i2c1)
light_sensor2 = bh1750.BH1750(i2c2)

globalVars.swHit = 0

CW = 0
CCW = 1
SPR = 200        #steps per revolution in full step mode
up = CCW
down = CW

led = Pin("LED", Pin.OUT)
EN = Pin(11, Pin.OUT)
SLP = Pin(13, Pin.OUT)
RST = Pin(12, Pin.OUT)
DIR = Pin(16, Pin.OUT)
STEP = Pin(17, Pin.OUT)
#initilialize motor
EN.high()
SLP.high()
RST.high()
DIR.value(up)
led.low()

total_rotations = 20
total_steps = SPR*total_rotations    #200*20 = 4000
rpm = 60
stepDelay = int(((30)/(rpm*SPR))*(10**6)) #microseconds, 7.5 ms/step, delay=3.75ms
print(stepDelay)
rest = 10 #How long to rest between each findLight

def RotateMotor(direction, delay, steps):
    MM = 0
    for x in range(steps):
        #check manual mode flag
        if globalVars.manualMode:
            manualMotor.rotateMotor_manual()
            MM = 1
            break
        
        #if switch hit and interrupt, stop motor movement
        if globalVars.swHit==1 and direction==down:
            break
        elif globalVars.swHit==2 and direction==up:
            break
        elif globalVars.swHit==1 and direction==up:
            EN.low()
            globalVars.swHit = 0
        elif globalVars.swHit==2 and direction==down:
            EN.low()
            globalVars.swHit = 0
            
        if not ((globalVars.swHit==1 and direction==down) or (globalVars.swHit==2 and direction==up)):
            DIR.value(direction)
            STEP.high()
            time.sleep_us(delay)
            #time.sleep(delay)
            STEP.low()
            time.sleep_us(delay)
            #time.sleep(delay)
            
            if direction == up:
                globalVars.currSteps += 1
            else:
                globalVars.currSteps -= 1
       
    return MM


#Lux noise threshold, move adjust reflectors if change in lux is greater than this
luxNzThrs = 30

def findLight(direction, stepDelay):
    #check manual mode flag
    if globalVars.manualMode:
        manualMotor.rotateMotor_manual()
        return direction
    EN.low()
    lux1 = light_sensor1.luminance(bh1750.BH1750.CONT_HIRES_1)
#     light_sensor2.set_mode(bh1750.BH1750.CONT_HIRES_1)
    lux2 = light_sensor2.luminance(bh1750.BH1750.ONCE_HIRES_1)
    prevLux = (lux1+lux2)/2
#     prevLux = lux2

    #direction = up      #Need to check if CW corresponds to up, start findLight routine when reflectors are at bottom
    baseSteps = 700    #Number of steps to rotate initially for finding light, decreases as direction changes, to hone in
    steps = baseSteps
    print("currSteps: ", globalVars.currSteps)
    print("direction: ", direction)
    MM = RotateMotor(direction, stepDelay, steps)
    if MM:
        return direction
    print("currSteps: ", globalVars.currSteps)
    lux1 = light_sensor1.luminance(bh1750.BH1750.CONT_HIRES_1)
    lux2 = light_sensor2.luminance(bh1750.BH1750.CONT_HIRES_1)
    lux = (lux1+lux2)/2
    #lux = lux2
    
    while True:
        #check manual mode flag
        if globalVars.manualMode:
            manualMotor.rotateMotor_manual()
            break
        #Motor active
        EN.low()
        #"Borrow" from the queue in case interrupted
        
        if globalVars.swHit==0:
            #optimal spot not found yet
            print("lux-prevLux: ", lux-prevLux)
            if fabs(lux - prevLux) > (luxNzThrs):
                if lux > prevLux:
                    #Continue in the direction that reflectors were already moving
                    MM = RotateMotor(direction, stepDelay, steps)
                    if MM:
                        break
                else:
                    #Reverse reflector direction and reduce amount reflectors move
                    direction = ~direction
                    steps = floor(0.75*steps)
                    MM = RotateMotor(direction, stepDelay, steps)
                    if MM:
                        break
            #optimal spot found
            else:
                #reset rotation amount to full amount for the next time reflectors need to find light
                steps = baseSteps
                break
        
        #If reflectors at limits
        elif globalVars.swHit==1 or globalVars.swHit==2:
            #reverse direction
            print("change dir")
            if (globalVars.swHit==1):
                direction = up
            elif (globalVars.swHit==2):
                direction = down
            #direction = ~direction
            #optimal spot not found yet, go reverse direction, no longer at limit
            if fabs(lux - prevLux) > luxNzThrs:
                if lux < prevLux:
                    MM = RotateMotor(direction, stepDelay, steps)
                    globalVars.swHit = 0
                    if MM:
                        break
            else:
                #stay at limit, begin going away from limit at next check
                break
        
        prevLux = lux
        # Measure the ambient light in lux
        lux1 = light_sensor1.luminance(bh1750.BH1750.CONT_HIRES_1)
        lux2 = light_sensor2.luminance(bh1750.BH1750.CONT_HIRES_1)
        lux = (lux1+lux2)/2
        #print(f"Ambient light level: {lux} lux")
        #lux = lux2
        
    return direction
            
            
def posRst():
    print("Initializing")
    
    while globalVars.swHit==0:
        #check manual mode flag
        if globalVars.manualMode:
            manualMotor.rotateMotor_manual()
        
        globalVars.currSteps = 2*total_steps
        RotateMotor(down, stepDelay, 200)

    globalVars.currSteps = 0
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

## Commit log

2023-11-11 Pico w was able to make post request to cloud atlas database
2024-03-15 RTC_wifi and overall structure of motor control
2024-03-16 Fixed network connection issue, add LED indications
    [RTC_wifi.py, main.py]
2024-03-27 added pico files
2024-04-10 Auto rotate based on light maximizing. Interrupts in limSwitch, asynchronous cooperative multitasking between manualMotor and lightTrackerMain, motor disabled when not in use. In testing.
2024-04-10 removed queue, replace with global variable currSteps in limSwitch. Will replace cooperative multitasking with interrupts for activating manualMotor
    [lightTrackerMain.py, limSwitch.py, main.py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]
2024-04-11 Replaced cooperative multitasking for manual mode with an interrupt. Not yet tested.
    [limSwitch.py, main.py, manualMotor.py]
2024-04-11 Fixed bugs with new infrastructure. Need to incorporate light sensor data sending next.
    [limSwitch.py, main.py, manualMotor.py]
2024-04-16 Combined motor control and light data-sending code
2024-04-17 Fixed issues from physical testing, 4/16
    [limSwitch.py, lux_sensor_main.py, main.py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]
2024-04-20 Removed duplicate function definitions in temperature_current_main.py, main.py is the same as temperature_current_main.py
2024-04-27 Added readme & files
    [Bottom Plate v13.stl, Motor Mount v16.stl, Rod Fastener v9.stl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]
2024-04-27 Added PCB notes
2024-04-27 Added printing settings
2024-04-27 Moved pico web server folder to working files folder
2024-04-27 Fixed flow diagram issues
